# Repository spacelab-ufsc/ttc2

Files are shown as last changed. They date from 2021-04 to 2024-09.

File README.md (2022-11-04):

<h1 align="center">
    TELEMETRY, TRACKING AND COMMAND 2.0
    <br>
</h1>

<h4 align="center">Telemetry, Tracking and Command module (version 2) designed and developed by SpaceLab.</h4>

<p align="center">
    <a href="https://github.com/spacelab-ufsc/spacelab#versioning">
        
    </a>
    <a href="https://github.com/spacelab-ufsc/ttc2/releases">
        
    </a>
    <a href="https://github.com/spacelab-ufsc/ttc2/releases">
        
    </a>
    <a href="https://github.com/spacelab-ufsc/ttc2/commits/master">
        
    </a>
    <a href="https://github.com/spacelab-ufsc/ttc2/issues">
        
    </a>
    <a href="https://github.com/spacelab-ufsc/ttc2/graphs/contributors">
        
    </a>
</p>

<p align="center">
    <a href="#overview">Overview</a> •
    <a href="#license">License</a> •
    <a href="#releases">Releases</a> •
</p>

<p align="center">
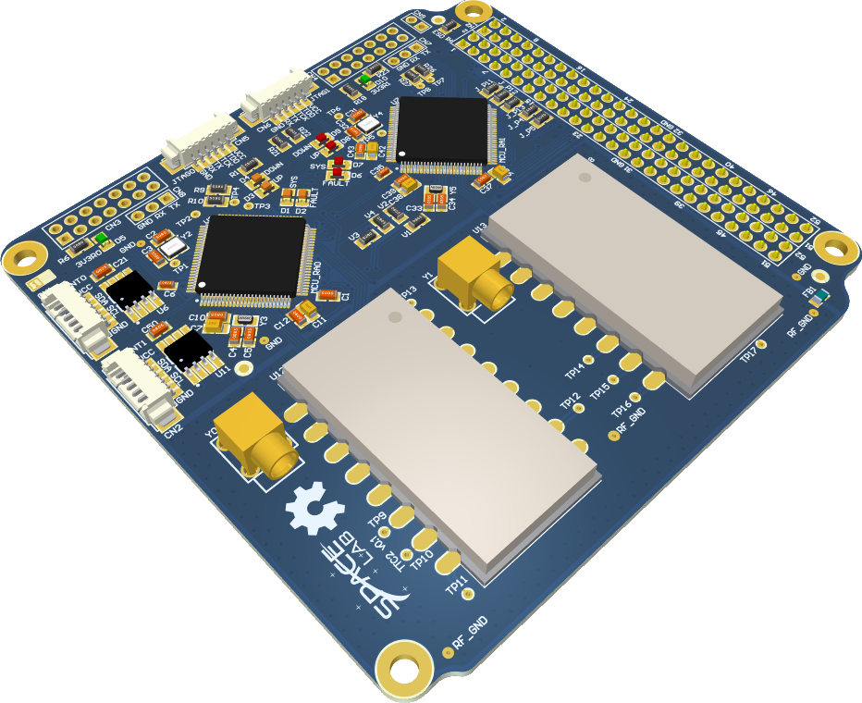
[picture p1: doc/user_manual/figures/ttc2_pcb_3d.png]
    
</p>

## Overview

The TTC (or TT&C) is the second generation communication module of the CubeSats from SpaceLab. It is responsible to make the communication between the earth (a ground station) and a satellite, and is divided in two sub-modules: Beacon and downlink/uplink.

## License

This project is open-source under three different licenses: GNU General Public License v3.0 for firmware sources, CERN Open Hardware License v2.0 for hardware files, and CC BY-SA 4.0 for the documentation. Some third-part files and libraries are subjected to their specific terms and licenses.

## Releases

The TTC 2.0 software and hardware releases are synchronized in order to garantee compatibility. Then, using diferent versions might lead to unpredictable behavior. Refer to the [documentation](https://github.com/spacelab-ufsc/ttc2/tree/master/doc) for compatibility notes.

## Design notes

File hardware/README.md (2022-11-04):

<h1 align="center">
    TTC2 HARDWARE
    <br>
</h1>

<h4 align="center">Telemetry, Tracking and Command module hardware project (sources, outputs, and documentation).</h4>

<p align="center">
    <a href="https://github.com/spacelab-ufsc/spacelab#versioning">
        
    </a>
    <a href="https://github.com/spacelab-ufsc/ttc2/releases">
        
    </a>
    <a href="https://github.com/spacelab-ufsc/ttc2/releases">
        
    </a>
    <a href="https://github.com/spacelab-ufsc/ttc2/commits/master">
        
    </a>
    <a href="https://github.com/spacelab-ufsc/ttc2/issues">
        
    </a>
    <a href="">
        
    </a>
    <a href="#license">
        
    </a>
    <a href="https://github.com/floripasat/ttc">
        
    </a>
</p>

<p align="center">
    <a href="#overview">Overview</a> •
    <a href="#architecture">Architecture</a> •
    <a href="#development">Development</a> •
    <a href="#version">Version</a> •
    <a href="#license">License</a> •
    <a href="#notes">Notes</a>
</p>

<p align="center">
    
    
</p>

## Overview

## Architecture

## Development

#### Manufacture

The folder [fabrication](https://github.com/spacelab-ufsc/ttc2/tree/master/hardware/fabrication) contain 3 "ready to go" files: the gerbers and nc_drills for manufacturing the board, the BOM with all required components, and the pick_place file for automated assembly. Additional files are avaliable in the [outputs](https://github.com/spacelab-ufsc/ttc2/tree/master/hardware/outputs) folder, which contain several useful files and documents, such as: 3D models, bill of materials, schematics, layout prints, and draftsman.

#### Assembly

The board has components that should not be soldered simultaneously. Refer to the [documentation](https://github.com/spacelab-ufsc/ttc2/tree/master/doc) in the "Assembly" chapter.

#### Power-on procedure

The board requires external supply from the PC-104 connector or the JTAG programmer interface. The following diagram present a simplified diagram of the board power. Refer to the [documentation](https://github.com/spacelab-ufsc/ttc2/tree/master/doc) in the "Instructions" chapter. 

#### Debugging

The debugging is performed through a serial UART port, using as default a baud rate of 115200, 1 stop bit, and no parity bit. The interface uses a log system standard to improve readability. Refer to the [documentation](https://github.com/spacelab-ufsc/obdh2/tree/master/doc) in the "Instructions" chapter.  

#### Testing

Automated testing is not avaliable yet.  

## Version

Refer to the [releases](https://github.com/spacelab-ufsc/ttc2/releases) page.

## License

This repository containing hardware files is licensed under CERN Open Hardware License, version 2.

## Notes

Project under development!

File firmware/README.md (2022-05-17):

<h1 align="center">
    <br>
    TTC 2.0 FIRMWARE
    <br>
</h1>

<h4 align="center">Telemetry, Tracking and Command module firmware project (sources, configs and documentation).</h4>

<p align="center">
    <a href="https://github.com/spacelab-ufsc/spacelab#versioning">
        
    </a>
    <a href="https://github.com/spacelab-ufsc/ttc2/releases">
        
    </a>
    <a href="https://github.com/spacelab-ufsc/ttc2/blob/dev_firmware/firmware/version.h">
        
    </a>
    <a href="https://github.com/spacelab-ufsc/ttc2/commits/master">
        
    </a>
    <a href="">
        
    </a>
    <a href="https://github.com/spacelab-ufsc/ttc2/blob/master/firmware/main.c">
        
    </a>
    <a href="">
        
    </a>
    <a href="#license">
        
    </a>
    <a href="https://github.com/spacelab-ufsc/ttc2/actions">
        
    </a>
</p>

<p align="center">
    <a href="#overview">Overview</a> •
    <a href="#dependencies">Dependencies</a> •
    <a href="#development">Development</a> •
    <a href="#version">Version</a> •
    <a href="#license">License</a>
</p>

<br>

## Overview

The TTC 2.0 board has two MSP430 low-power microcontrollers that runs the firmware application. It manages the others sub-modules within the board, synchronizes actions, handles communication with the Earth's segment, and manages the data flow. The programming language used is C and firmware was developed in the Code Composer Studio IDE (a.k.a. CCS). 

## Dependencies

* MSP430 DriverLib v2.91.11.01

## Development

#### Toolchain setup

The Code Composer Studio (CCS) v9.0, or later, can be downloaded [here](http://software-dl.ti.com/ccs/esd/documents/ccs_downloads.html). After downloaded, start the install process. For the TTC 2.0, only the *MSP430 Ultra Low Power MCUs* package is required. More instructions for Linux environment, click [here](https://software-dl.ti.com/ccs/esd/documents/ccs_linux_host_support.html).

#### Compiling and building
	
Clone [this repository](https://github.com/spacelab-ufsc/ttc2.git). After this, import the source project into CCS:
`File -> Import -> Code Composer Studio -> CCS Projects -> Select the source folder: ttc/firmware -> Leave 'Copy projects into workspace' unchecked / Finish`. Then, click in the Build button or press "Ctrl+B" to compile and build the sources. 

> Alternatively, it is possible to use the available makefile to import, compile and build the firmware in the linux environment. It is necessary to update the directories to correspond to those in the running machine, hit "make import" in the linux terminal and hit "make".

#### Debugging

Before deploying the program into the microcontroller using the JTAG interface, follow the [power-on procedures](https://github.com/spacelab-ufsc/ttc2/tree/dev_hardware/hardware#power-on-procedure). Using the [MSP-FET](http://www.ti.com/tool/MSP-FET) is possible to program the microcontroller and start a debug session, which allows full control of the firmware in execution. For that, with the project opened in the CCS, click in the "Debug" button or press "F11" to upload the code into the TTC 2.0 board.

Besides the JTAG, there is the debugging performed through a serial UART port, using as default a baud rate of 115200, 1 stop bit, and no parity bit. The interface uses a log system standard to improve readability. Refer to the [documentation](https://github.com/spacelab-ufsc/ttc2/tree/master/doc) in the "Instructions" chapter.

> Alternatively, it is possible to use the available makefile to perform the deployment of the firmware image into the microcontroller in the linux environment using the MSP-FET. It is necessary to follow the power-on procedures, connect the programmer and hit "make flash" in the terminal.

## Version

Refer to the [releases](https://github.com/spacelab-ufsc/ttc2/releases) page and the [version](https://github.com/spacelab-ufsc/ttc2/blob/master/firmware/version.h) file.

## License

The firmware of this project is licensed under GPLv3 license.

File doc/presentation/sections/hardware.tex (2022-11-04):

%
% design.tex
%
% Copyright (C) 2022 by SpaceLab.
%
% TTC 2.0 Critical Design Review
%
% This work is licensed under the Creative Commons Attribution-ShareAlike 4.0
% International License. To view a copy of this license,
% visit http://creativecommons.org/licenses/by-sa/4.0/.
%

%
% \brief Design slides.
%
% \author Gabriel Mariano Marcelino <gabriel.mm8@gmail.com>
% \author Miguel Boing <miguelboing13@gmail.com>
%
% \version 0.1.0
%
% \date 2022/07/28
%

\begin{frame}{Specifications}

    \begin{itemize}
        \item \textbf{Microcontroller}: MSP430F6659/MSP430F5659
        \item \textbf{Clock}: 32 MHz
        \item \textbf{Memories}:
        \begin{itemize}
            \item \textit{RAM}: 64 kB (SRAM)
            \item \textit{Flash}: 512 kB (code)
        \end{itemize}
        \item \textbf{Sensors}: Voltage, current and temperature
        \item \textbf{Modulation}: (G)FSK or (G)MSK
        \item \textbf{Baudrate}: 1200 to 9600 bps
        \item \textbf{Frequency}: 145-146 MHz, 435-438 MHz or 450 MHz bands
        \item \textbf{Protocol}: NGHam
        \item \textbf{Interfaces}: UART, I$^{2}$C and SPI
        \item \textbf{Mass}: 73 g
        \item PC-104 compatible
    \end{itemize}

\end{frame}

% #########################################################################
% #########################################################################

\begin{frame}{Electrical Block Diagram}

    \begin{figure}[!ht]
        \begin{center}
            
        \end{center}
    \end{figure}

\end{frame}

\begin{frame}{Schematics}

    Available at: \href{https://github.com/spacelab-ufsc/ttc2/tree/master/hardware/outputs/board_schematics}{\textcolor{blue}{\underline{https://github.com/spacelab-ufsc/ttc2}}}

    \begin{figure}[!ht]
        \begin{center}
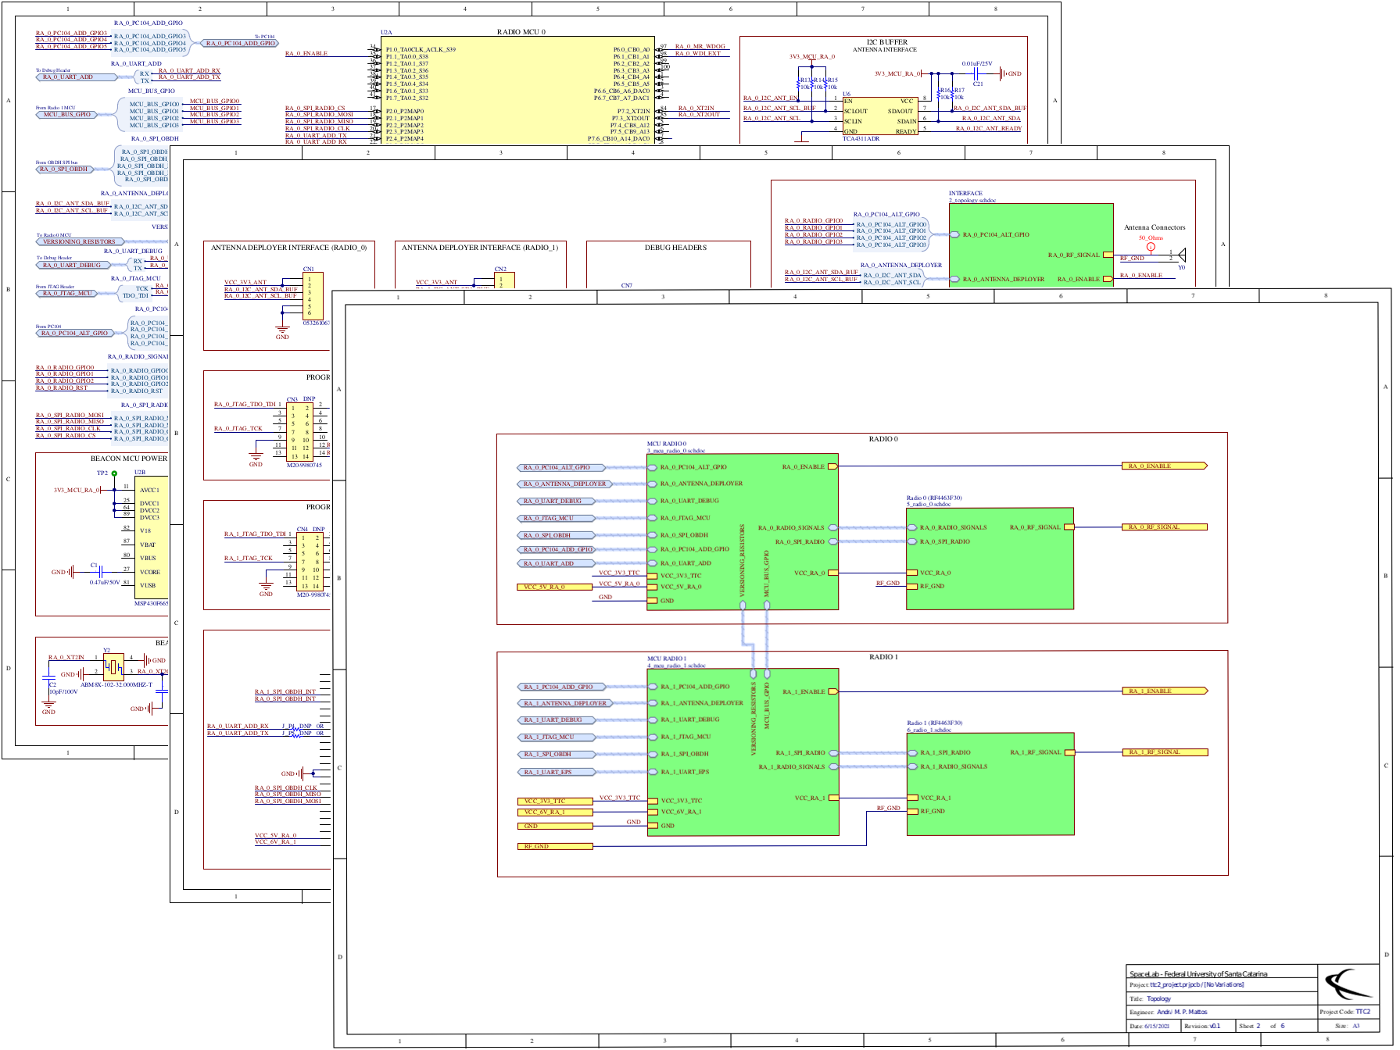
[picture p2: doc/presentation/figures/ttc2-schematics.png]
            
        \end{center}
    \end{figure}

\end{frame}

\begin{frame}{PCB Layout}

    Available at: \href{https://github.com/spacelab-ufsc/ttc2/tree/master/hardware/sources}{\textcolor{blue}{\underline{https://github.com/spacelab-ufsc/ttc2}}}

    \begin{columns}[t]
        \begin{column}[t]{0.5\textwidth}
            \begin{figure}[!ht]
                \begin{center}
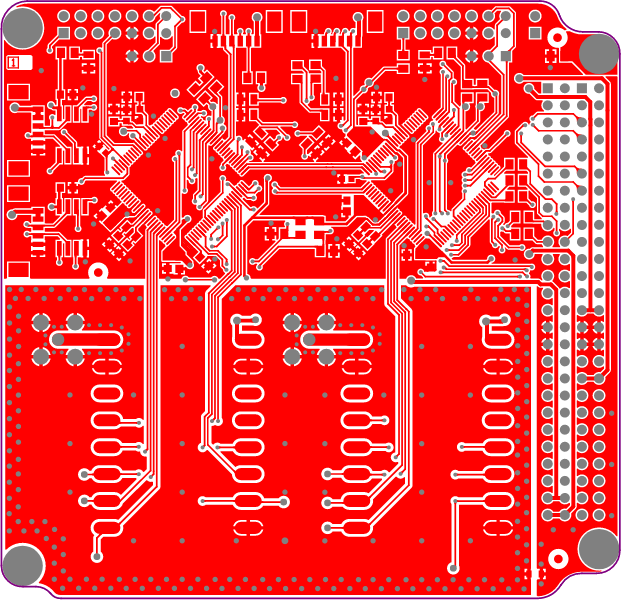
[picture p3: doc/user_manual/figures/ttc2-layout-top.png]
                    
                \end{center}
                \caption{Top side}
            \end{figure}
        \end{column}
        \begin{column}[t]{0.5\textwidth}
            \begin{figure}[!ht]
                \begin{center}
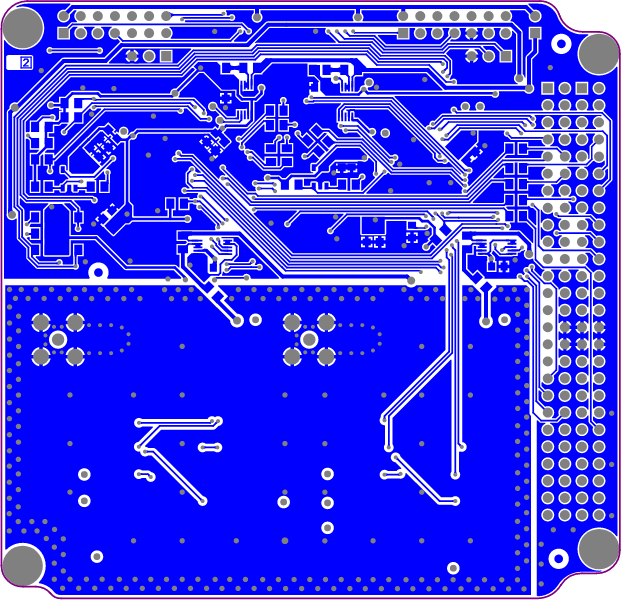
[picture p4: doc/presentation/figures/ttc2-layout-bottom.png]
                    
                \end{center}
                \caption{Bottom side}
            \end{figure}
        \end{column}
    \end{columns}

\end{frame}

\begin{frame}{3D Model}

    Available at: \href{https://github.com/spacelab-ufsc/ttc2/tree/master/hardware/outputs/board_3dmodels}{\textcolor{blue}{\underline{https://github.com/spacelab-ufsc/ttc2}}}

    \begin{figure}[!ht]
        \begin{center}
            
        \end{center}
    \end{figure}

\end{frame}

% #########################################################################
% #########################################################################

\begin{frame}{Power Consumption}

    \begin{itemize}
        \item Three separated voltage inputs: 3V3, 5V and 6V (microcontrollers and transceivers)
        \vspace{0.5cm}
        \item Power consumption\footnote{For one transceiver (there is two in TTC 2.0)}:
            \begin{itemize}
                \item Stand-by mode $\cong$ 83 mW
                \vspace{0.3cm}
                \item Transmission mode $\cong$ 2800 mW
                \vspace{0.3cm}
                \item Reception mode $\cong$ 163 mW
            \end{itemize}
    \end{itemize}

\end{frame}

% #########################################################################
% #########################################################################

\begin{frame}{Electrical Interfaces: PC-104}

\begin{table}[!h]\tiny
    \centering
    \begin{tabular}{cllll}
        \toprule[1.5pt]
        \textbf{Pin [A-B]} & \textbf{H1A}     & \textbf{H1B}     & \textbf{H2A}  & \textbf{H2B}  \\
        \midrule
        1-2                & -                & -                & -                & -                \\
        3-4                & -                & -                & -                & -                \\
        5-6                & -                & -                & RA\_1\_UART\_RX  & -                \\
        7-8                & GPIO\_6          & GPIO\_7          & RA\_1\_UART\_TX  & GPIO\_0          \\
        9-10               & RA\_1\_SPI\_INT  & RA\_1\_EN        & -                & -                \\
        11-12              & RA\_0\_SPI\_INT  & RA\_0\_EN        & RA\_1\_SPI\_MOSI & RA\_1\_SPI\_CLK  \\
        13-14              & -                & -                & RA\_1\_SPI\_CS   & RA\_1\_SPI\_MISO \\
        15-16              & -                & -                & -                & -                \\
        17-18              & -                & -                & -                & GPIO\_1          \\
        19-20              & -                & GPIO\_2          & -                & GPIO\_3          \\
        21-22              & -                & -                & -                & GPIO\_4          \\
        23-24              & -                & -                & -                & -                \\
        25-26              & -                & -                & -                & -                \\
        27-28              & -                & -                & VCC\_3V3         & VCC\_3V3         \\
        29-30              & GND              & GND              & GND              & GND              \\
        31-32              & GND              & GND              & GND              & GND              \\
        33-34              & -                & -                & -                & -                \\
        35-36              & RA\_0\_SPI\_CLK  & -                & VCC\_3V3\_ANT    & VCC\_3V3\_ANT    \\
        37-38              & RA\_0\_SPI\_MISO & -                & -                & -                \\
        39-40              & RA\_0\_SPI\_MOSI & RA\_0\_SPI\_CS   & -                & -                \\
        41-42              & -                & -                & -                & GPIO\_5          \\
        43-44              & -                & -                & -                & -                \\
        45-46              & -                & -                & -                & -                \\
        47-48              & -                & -                & -                & -                \\
        49-50              & VCC\_5V\_RA\_0   & VCC\_5V\_RA\_0   & -                & -                \\
        51-52              & VCC\_6V\_RA\_1   & VCC\_6V\_RA\_1   & -                & -                \\
        \bottomrule[1.5pt]
    \end{tabular}
    \label{tab:pc104-pins}
\end{table}

\end{frame}

\begin{frame}{Other Electrical Interfaces}

    \begin{table}[!htb]\tiny
        \centering
        \label{tab:icd}
        \begin{tabular}{lccl}
            \toprule[1.5pt]
            \textbf{Connector} & \textbf{Interface} & \textbf{Type} & \textbf{Pins} \\
            \midrule
            \multirow{6}{*}{CN1} & \multirow{6}{*}{I$^{2}$C} & \multirow{6}{*}{PicoBlade} & 3V3 \\
                                 &                           &                            & 3V3 \\
                                 &                           &                            & I2C\_SDA \\
                                 &                           &                            & I2C\_SCL \\
                                 &                           &                            & GND \\
                                 &                           &                            & GND \\
            \midrule
            \multirow{6}{*}{CN2} & \multirow{6}{*}{I$^{2}$C} & \multirow{6}{*}{PicoBlade} & 3V3 \\
                                 &                           &                            & 3V3 \\
                                 &                           &                            & I2C\_SDA \\
                                 &                           &                            & I2C\_SCL \\
                                 &                           &                            & GND \\
                                 &                           &                            & GND \\
            \bottomrule[1.5pt]
        \end{tabular}
    \end{table}

\end{frame}

\begin{frame}{Other Electrical Interfaces}

    \begin{table}[!htb]\tiny
        \centering
        \label{tab:icd}
        \begin{tabular}{lccl}
            \toprule[1.5pt]
            \textbf{Connector} & \textbf{Interface} & \textbf{Type} & \textbf{Pins} \\
            \midrule
            \multirow{14}{*}{CN3} & \multirow{14}{*}{JTAG} & \multirow{14}{*}{Pin Header} & TDO\_TDI \\
                                  &                        &                              & 3V3 \\
                                  &                        &                              & None \\
                                  &                        &                              & None \\
                                  &                        &                              & None \\
                                  &                        &                              & None \\
                                  &                        &                              & TCK \\
                                  &                        &                              & None \\
                                  &                        &                              & GND \\
                                  &                        &                              & None \\
                                  &                        &                              & None \\
                                  &                        &                              & UART\_TX \\
                                  &                        &                              & None \\
                                  &                        &                              & UART\_RX \\

            \bottomrule[1.5pt]
        \end{tabular}
    \end{table}

\end{frame}

\begin{frame}{Other Electrical Interfaces}

    \begin{table}[!htb]\tiny
        \centering
        \label{tab:icd}
        \begin{tabular}{lccl}
            \toprule[1.5pt]
            \textbf{Connector} & \textbf{Interface} & \textbf{Type} & \textbf{Pins} \\
            \midrule
            \multirow{14}{*}{CN4} & \multirow{14}{*}{JTAG} & \multirow{14}{*}{Pin Header} & TDO\_TDI \\
                                  &                        &                              & 3V3 \\
                                  &                        &                              & None \\
                                  &                        &                              & None \\
                                  &                        &                              & None \\
                                  &                        &                              & None \\
                                  &                        &                              & TCK \\
                                  &                        &                              & None \\
                                  &                        &                              & GND \\
                                  &                        &                              & None \\
                                  &                        &                              & None \\
                                  &                        &                              & UART\_TX \\
                                  &                        &                              & None \\
                                  &                        &                              & UART\_RX \\

            \bottomrule[1.5pt]
        \end{tabular}
    \end{table}

\end{frame}

\begin{frame}{Other Electrical Interfaces}

    \begin{table}[!htb]\tiny
        \centering
        \label{tab:icd}
        \begin{tabular}{lccl}
            \toprule[1.5pt]
            \textbf{Connector} & \textbf{Interface} & \textbf{Type} & \textbf{Pins} \\
            \midrule
            \multirow{6}{*}{CN5} & \multirow{6}{*}{JTAG} & \multirow{6}{*}{PicoBlade} & 3V3 \\
                                 &                       &                            & TDO\_TDI \\
                                 &                       &                            & TCK \\
                                 &                       &                            & UART\_TX \\
                                 &                       &                            & UART\_RX \\
                                 &                       &                            & GND \\
            \midrule
            \multirow{6}{*}{CN6} & \multirow{6}{*}{JTAG} & \multirow{6}{*}{PicoBlade} & 3V3 \\
                                 &                       &                            & TDO\_TDI \\
                                 &                       &                            & TCK \\
                                 &                       &                            & UART\_TX \\
                                 &                       &                            & UART\_RX \\
                                 &                       &                            & GND \\
            \midrule
            \multirow{3}{*}{CN7} & \multirow{3}{*}{UART} & \multirow{3}{*}{PinHeader} & TX \\
                                 &                       &                            & RX \\
                                 &                       &                            & GND \\
            \midrule
            \multirow{3}{*}{CN8} & \multirow{3}{*}{UART} & \multirow{3}{*}{PicoBlade} & TX \\
                                 &                       &                            & RX \\
                                 &                       &                            & GND \\
            \midrule
            \multirow{2}{*}{CN9} & \multirow{2}{*}{Jumper} & \multirow{2}{*}{Pin Header} & 3V3 \\
                                 &                         &                      & - \\
            \bottomrule[1.5pt]
        \end{tabular}
    \end{table}

\end{frame}

\begin{frame}{Other Electrical Interfaces}

    \begin{table}[!htb]\tiny
        \centering
        \label{tab:icd}
        \begin{tabular}{lccl}
            \toprule[1.5pt]
            \textbf{Connector} & \textbf{Interface} & \textbf{Type} & \textbf{Pins} \\
            \midrule
            \multirow{2}{*}{Y0} & \multirow{2}{*}{RF} & \multirow{2}{*}{MCX} & RF\_SIGNAL \\
                                &                     &                      & RF\_GND \\
            \midrule
            \multirow{2}{*}{Y1} & \multirow{2}{*}{RF} & \multirow{2}{*}{MCX} & RF\_SIGNAL \\
                                &                     &                      & RF\_GND \\
            \bottomrule[1.5pt]
        \end{tabular}
    \end{table}

\end{frame}

\begin{frame}{Dimensions}

    \begin{figure}[!ht]
        \begin{center}
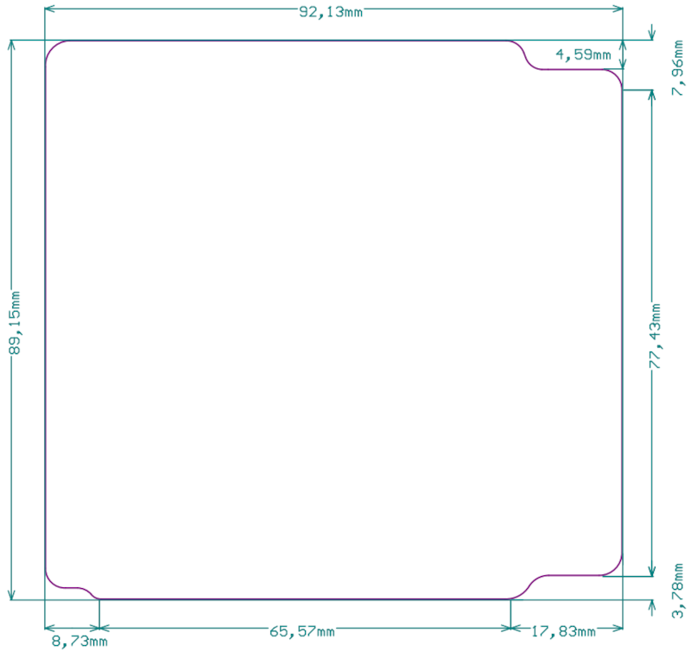
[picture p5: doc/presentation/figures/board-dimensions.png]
            
        \end{center}
    \end{figure}

\end{frame}

\begin{frame}{Voltage/Current Sensors}

    \begin{itemize}
        \item Voltage, current and power sensor
        \vspace{0.3cm}
        \item Quantity: 4 (one per radio module and one per microncontroller circuit)
        \vspace{0.3cm}
        \item Texas Instruments INA226AQDGSRQ1
        \vspace{0.3cm}
        \item I$^{2}$C Interface
        \vspace{0.3cm}
    \end{itemize}

\end{frame}

\begin{frame}{External Watchdog}

    \begin{itemize}
        \item IC: Texas Instruments TPS3823
        \vspace{0.5cm}
        \item Voltage monitor with a watchdog timer feature
        \vspace{0.5cm}
        \item Timeout period: $1600\ ms$
        \vspace{0.5cm}
        \item Reset period: $100\ ms$
    \end{itemize}

\end{frame}

\begin{frame}{Transceiver}

    \begin{itemize}
        \item \href{https://www.nicerf.com/products/detail/1w-rf-module-rf4463f30.html}{\textcolor{blue}{\underline{NiceRF RF4463F30}}}
        \item Based on \href{https://www.silabs.com/wireless/proprietary/ezradiopro-sub-ghz-ics/device.si4463?tab=specs}{\textcolor{blue}{\underline{Si4463}}} transceiver
        \item Integrated power amplifier and RF switch (single antenna)
        \item Half-Duplex
        \item Output power: 30 dBm
        \item SPI Interface
    \end{itemize}
    \begin{figure}[!ht]
        \begin{center}
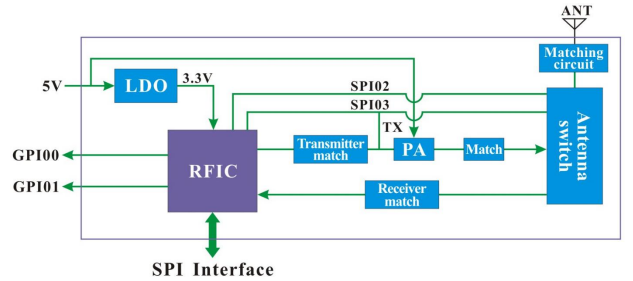
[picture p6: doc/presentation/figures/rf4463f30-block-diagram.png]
            
        \end{center}
    \end{figure}

\end{frame}

\begin{frame}{Flight Model Specs. and Preparation}

    \begin{itemize}
        \item \textbf{PCB specs.}: IPC 6012 Class 3
        \vspace{0.3cm}
        \item \textbf{PCB thickness}: 1,6 mm
        \vspace{0.3cm}
        \item \textbf{Material}: TG170 FR-4
        \vspace{0.3cm}
        \item \textbf{Surface finish}: ENIG
        \vspace{0.3cm}
        \item \textbf{Board finish}: Conformal coating application
    \end{itemize}

\end{frame}

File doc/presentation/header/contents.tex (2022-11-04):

%
% contents.tex
%
% Copyright (C) 2022 by SpaceLab.
%
% TTC 2.0 Module
%
% This work is licensed under the Creative Commons Attribution-ShareAlike 4.0
% International License. To view a copy of this license,
% visit http://creativecommons.org/licenses/by-sa/4.0/.
%

%
% \brief Table of contents.
%
% \author Gabriel Mariano Marcelino <gabriel.mm8@gmail.com>
% \author Miguel Boing <miguelboing13@gmail.com>
%
% \version 0.1.0
%
% \date 2022/06/24
%

\begin{frame}
    \frametitle{Summary}
    \tableofcontents
\end{frame}

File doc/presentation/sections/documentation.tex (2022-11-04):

%
% documentation.tex
%
% Copyright (C) 2022 by SpaceLab.
%
% TTC 2.0 Module
%
% This work is licensed under the Creative Commons Attribution-ShareAlike 4.0
% International License. To view a copy of this license,
% visit http://creativecommons.org/licenses/by-sa/4.0/.
%

%
% \brief Documentation slides.
%
% \author Gabriel Mariano Marcelino <gabriel.mm8@gmail.com>
% \author Miguel Boing <miguelboing13@gmail.com>
%
% \version 0.1.0
%
% \date 2022/08/07
%

\begin{frame}{Documentation}

    \begin{itemize}
        \item User manual (PDF)
        \vspace{0.4cm}
        \item This presentation
        \vspace{0.4cm}
        \item Schematics
        \vspace{0.4cm}
        \item Firmware: Doxygen
    \end{itemize}

\end{frame}

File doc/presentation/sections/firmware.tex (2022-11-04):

%
% firmware.tex
%
% Copyright (C) 2022 by SpaceLab.
%
% TTC 2.0 Module
%
% This work is licensed under the Creative Commons Attribution-ShareAlike 4.0
% International License. To view a copy of this license,
% visit http://creativecommons.org/licenses/by-sa/4.0/.
%

%
% \brief Firmware project slides.
%
% \author Gabriel Mariano Marcelino <gabriel.mm8@gmail.com>
% \author Miguel Boing <miguelboing13@gmail.com>
%
% \version 0.1.0
%
% \date 2022/07/28
%

\begin{frame}{Overview}

    \begin{columns}[t]
        \begin{column}[t]{0.6\textwidth}
            \begin{itemize}
                \vspace{1cm}
                \item Language: C
                \vspace{0.5cm}
                \item OS: FreeRTOS v10.2.1
            \end{itemize}
        \end{column}
        \begin{column}[t]{0.4\textwidth}
            \begin{figure}[!ht]
                \begin{center}
                    
                \end{center}
            \end{figure}
        \end{column}
    \end{columns}

\end{frame}

% #########################################################################
% #########################################################################

\begin{frame}{System Tasks}

\begin{table}[!h]\scriptsize
    \centering
    \label{tab:firmware-tasks}
    \begin{tabular}{lccccc}
        \toprule[1.5pt]
        \textbf{Name}          & \textbf{Priority} & \textbf{Initial delay [ms]} & \textbf{Period [ms]} & \textbf{Stack [bytes]} \\
        \midrule
        Command Processing     & Highest & 0     & 100       & 500 \\
        Heartbeat              & Lowest  & 0     & 500       & 160 \\
        Housekeeping           & Medium  & 2000  & 10000     & 160 \\
        Radio Reset            & High    & 60000 & 60000     & 128 \\
        Startup                & Medium  & 0     & Aperiodic & 128 \\
        System Reset           & Medium  & 0     & 36000000  & 128 \\
        Time Control           & Medium  & 1000  & 1000      & 128 \\
        Uplink                 & Highest & 2000  & 500       & 500 \\
        Watchdog Reset         & Lowest  & 0     & 100       & 150 \\
        \bottomrule[1.5pt]
    \end{tabular}
\end{table}

\end{frame}

\begin{frame}{System Tasks}

    \begin{itemize}
        \item \textbf{Command Processing}: Process incomming commands (physical interfaces).
        \item \textbf{Heartbeat}: Blinks a status LED at a rate of 1 Hz.
        \item \textbf{Housekeeping}: This task manages the general operation of
the TTC.
        \item \textbf{Radio Reset}: Resets the radio at 600 seconds.
        \item \textbf{Startup}: Initializes the TTC 2.0 module.
        \item \textbf{System Reset}: Resets the microcontroller by software at every 10 hours.
        \item \textbf{Time Control}: Manages the system time.
        \item \textbf{Uplink}: Monitors radio for upcoming packages and stores it in memory.
        \item \textbf{Watchdog Reset}: Resets the watchdog timers at every 100 miliseconds.
    \end{itemize}

 \end{frame}

% #########################################################################
% #########################################################################

\begin{frame}{System Parameters}

\begin{table}[!htb]\tiny
    \centering
    \label{tab:vars-and-pars}
    \begin{tabular}{cll}
        \toprule[1.5pt]
        \textbf{ID} & \textbf{Name/Description} & \textbf{Type}\\
        \midrule
        0   & Device ID (0xCC2A or 0xCC2B)                                      & uint16 \\
        1   & Hardware version                                                  & uint8 \\
        2   & Firmware version (ex.: ``v1.2.3''' = 0x00010203)                  & uint32 \\
        3   & Time counter in millseconds                                       & uint32 \\
        4   & Reset counter                                                     & uint16 \\
        5   & Last reset cause:                                                 & uint8 \\
        6   & Input voltage of the $\mu$C in mV                                 & uint16 \\
        7   & Input current of the $\mu$C in mA                                 & uint16 \\
        8   & Temperature of the $\mu$C in K                                    & uint16 \\
        9   & Input voltage of the radio in mV                                  & uint16 \\
        10  & Input current of the radio in mA                                  & uint16 \\
        11  & Temperature of the radio in K                                     & uint16 \\
        12  & Last valid command (uplink packet ID)                             & uint8 \\
        13  & RSSI of the last valid telecommand                                & uint16 \\
        14  & Temperature of the antenna module in K                            & uint16 \\
        15  & Antenna module status bits                                        & uint16 \\
        16  & Antenna deployment status                                         & uint8 \\
        17  & Antenna deployment hibernation                                    & uint8 \\
        18  & TX enable                                                         & uint8 \\
        19  & TX packet counter                                                 & uint32 \\
        20  & RX packet counter (valid packets)                                 & uint32 \\
        21  & TX packets available in the FIFO buffer                           & uint8 \\
        22  & RX packets available in the FIFO buffer                           & uint8 \\
        23  & Number of bytes of the first available packet in the RX buffer    & uint16 \\
        \bottomrule[1.5pt]
    \end{tabular}
\end{table}

\end{frame}

\begin{frame}{Commands}

\begin{table}[!htb]\scriptsize
    \centering
    \label{tab:vars-and-pars}
    \begin{tabular}{cll}
        \toprule[1.5pt]
        \textbf{ID} & \textbf{Command} & \textbf{Parameters}\\
        \midrule
        1   & Read parameter              & Parameter ID \\
        2   & Write parameter             & Parameter ID + Parameter value \\
        3   & Transmit packet             & Data to transmit (payload of the NGHam packet) \\
        4   & Read first available packet & None \\
        \bottomrule[1.5pt]
    \end{tabular}
\end{table}

\end{frame}

% #########################################################################
% #########################################################################

\begin{frame}{Development Environment}

    \begin{columns}[t]
        \begin{column}[t]{0.6\textwidth}
            \begin{itemize}
                \vspace{0.4cm}
                \item Hardware: Engineering Model (EM)
                \vspace{0.4cm}
                \item Programmer: Texas Instruments MSP-FET programmer
                \vspace{0.4cm}
                \item IDE/Compiler: Code Composer Studio
                \vspace{0.4cm}
            \end{itemize}
        \end{column}
        \begin{column}[t]{0.5\textwidth}
            \vspace{1cm}
            \begin{figure}[!ht]
                \begin{center}
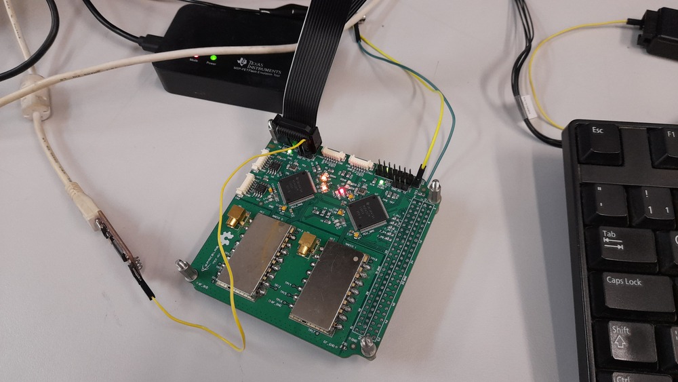
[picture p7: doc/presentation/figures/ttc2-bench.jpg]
                    
                \end{center}
            \end{figure}
        \end{column}
    \end{columns}

\end{frame}

% #########################################################################
% #########################################################################

\begin{frame}{Verification \& Validation}

    \begin{itemize}
        \item Unit tests framework: \href{https://cmocka.org/}{\textcolor{blue}{\underline{CMocka}}}
        \vspace{0.5cm}
        \item Static analysis tool: \href{https://cppcheck.sourceforge.io/}{\textcolor{blue}{\underline{CppCheck}}}
        \vspace{0.5cm}
        \item Code style standard: \href{https://www.misra.org.uk/}{\textcolor{blue}{\underline{MISRA-C 2012}}}
    \end{itemize}

\end{frame}

\begin{frame}{Verification \& Validation: TDD Flow}

    \begin{figure}[!ht]
        \begin{center}
            
        \end{center}
    \end{figure}

\end{frame}

\begin{frame}{Verification \& Validation: Development Flow}

    \begin{figure}[!ht]
        \begin{center}
            
        \end{center}
    \end{figure}

\end{frame}

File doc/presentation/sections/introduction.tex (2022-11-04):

%
% introduction.tex
%
% Copyright (C) 2022 by SpaceLab.
%
% TTC 2.0 Critical Design Review
%
% This work is licensed under the Creative Commons Attribution-ShareAlike 4.0
% International License. To view a copy of this license,
% visit http://creativecommons.org/licenses/by-sa/4.0/.
%

%
% \brief Introduction slides.
%
% \author Gabriel Mariano Marcelino <gabriel.mm8@gmail.com>
% \author Miguel Boing <miguelboing13@gmail.com>
%
% \version 0.1.0
%
% \date 2022/07/28
%

\begin{frame}{Overview}

    \begin{columns}[t]
        \begin{column}[t]{0.5\textwidth}
            \begin{itemize}
                \item Telemetry, Tracking and Command (TTC) module for small satellites like CubeSats
                \vspace{0.5cm}
                \item Project name: ``\textit{TTC 2.0}''
                \vspace{0.5cm}
                \item Fully open source
                \vspace{0.5cm}
                \item Based on FloripaSat-1 heritage
            \end{itemize}
        \end{column}
        \begin{column}[t]{0.5\textwidth}
            \begin{figure}[!ht]
                \begin{center}
                    
                \end{center}
            \end{figure}
        \end{column}
    \end{columns}

\end{frame}

% #########################################################################
% #########################################################################

\begin{frame}{Product Tree}

    \begin{figure}[!ht]
        \begin{center}
            
        \end{center}
    \end{figure}

\end{frame}

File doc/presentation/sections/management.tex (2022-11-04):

%
% management.tex
%
% Copyright (C) 2022 by SpaceLab.
%
% TTC 2.0 Critical Design Review
%
% This work is licensed under the Creative Commons Attribution-ShareAlike 4.0
% International License. To view a copy of this license,
% visit http://creativecommons.org/licenses/by-sa/4.0/.
%

%
% \brief Project management slides.
%
% \author Gabriel Mariano Marcelino <gabriel.mm8@gmail.com>
% \author Miguel Boing <miguelboing13@gmail.com>
%
% \version 0.1.0
%
% \date 2022/07/28
%

\begin{frame}{Project Management}

    \begin{itemize}
        \item Activities and tasks: Public GitHub issues/project
        \vspace{0.25cm}
        \item Source files and versioning control: \href{https://github.com/spacelab-ufsc/obdh2}{\textcolor{blue}{Git repository}} with three development branches:
            \begin{itemize}
                \item \textit{dev\_doc}: Documentation
                \item \textit{dev\_hardware}: Hardware project
                \item \textit{dev\_firmware}: Firmware project
            \end{itemize}
    \end{itemize}

    \begin{figure}[!ht]
        \begin{center}
            
        \end{center}
    \end{figure}

\end{frame}

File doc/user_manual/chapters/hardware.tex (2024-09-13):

%
% hardware.tex
%
% Copyright The TTC 2.0 Contributors.
%
% TTC 2.0 Documentation
%
% This work is licensed under the Creative Commons Attribution-ShareAlike 4.0
% International License. To view a copy of this license,
% visit http://creativecommons.org/licenses/by-sa/4.0/.
%

%
% \brief Hardware project chapter.
%
% \author Gabriel Mariano Marcelino <gabriel.mm8@gmail.com>
%
% \version 1.0.0
%
% \date 2021/04/02
%

\chapter{Hardware} \label{ch:hardware}

This chapter presents a description of the hardware project of the TTC 2.0 module. As the primary reference, a block diagram can be seen in \autoref{fig:hardware-diagram}. Also, a 3D model of both sides of the PCB is available in \autoref{fig:ttc2-3d-surface}.

\begin{figure}[!ht]
	\begin{center}
		
		\caption{Block diagram of the TTC 2.0 hardware.}
		\label{fig:hardware-diagram}
	\end{center}
\end{figure}

\begin{figure}[!ht]
    \begin{center}
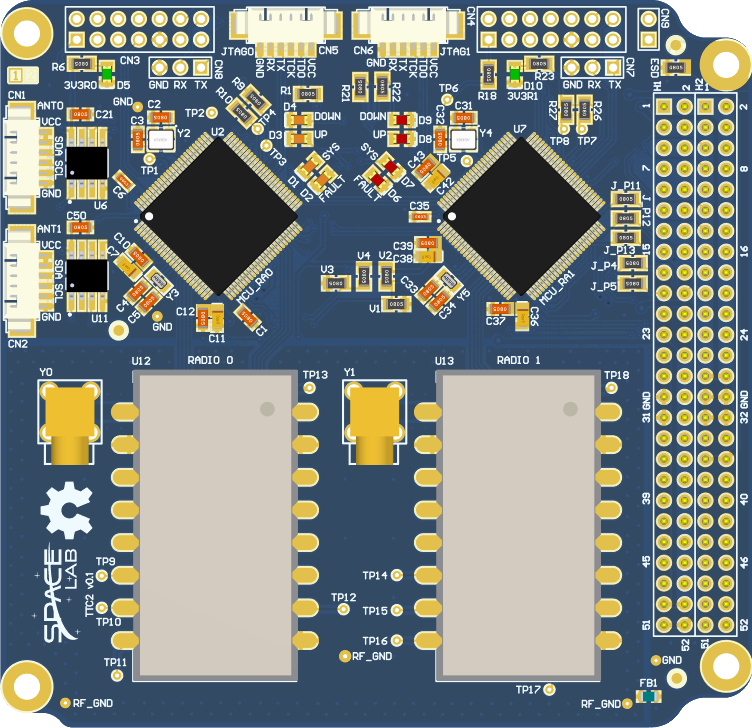
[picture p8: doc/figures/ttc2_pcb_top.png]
        \subfigure[Top side.\label{fig:ttc2-pcb-top}]{}
        ~
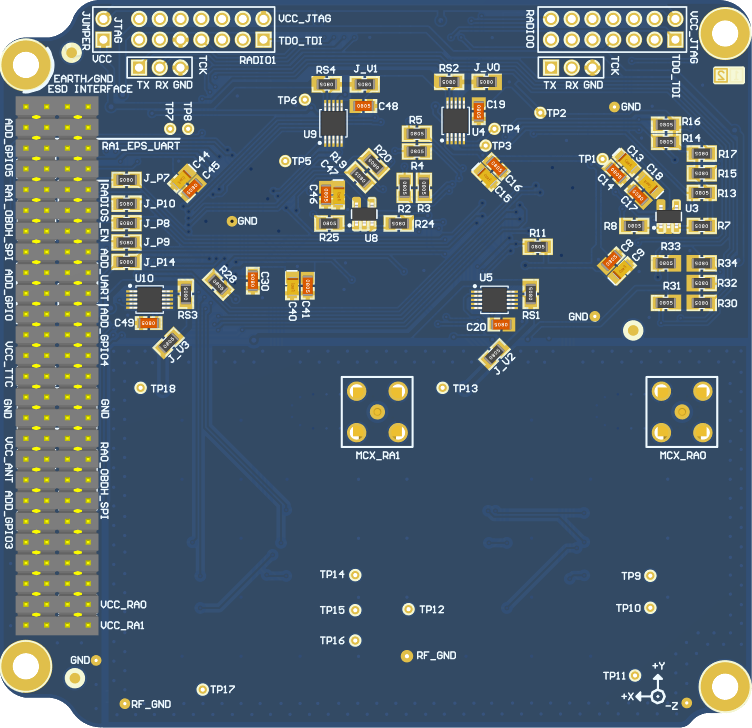
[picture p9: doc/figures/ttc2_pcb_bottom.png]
        \subfigure[Bottom side.\label{fig:ttc2-pcb-bottom}]{}
        \caption{Top and bottom sides of the TTC 2.0 board.}
        \label{fig:ttc2-3d-surface}
    \end{center}
\end{figure}

The following sections present a further description of the hardware project.

\section{Specifications}

The TTC 2.0 has two microcontrollers (MSP430FR6659) that run at a clock of 32 MHz, a RAM of 64 kB (SRAM), a flash memory of 512 kB for code storage, and another one of 128 kB for data storage. The TTC 2.0 also has current, voltage, and temperature sensors and two radio modules for RF communication. A brief description of the general specifications of the TTC 2.0 module is available below:

\begin{itemize}
    \item \textbf{Microcontroller}: MSP430F6659
    \item \textbf{Clock}: 32 MHz
    \item \textbf{Memories}:
    \begin{itemize}
        \item RAM: 64 kB (SRAM)
        \item Flash: 512 kB (code) and 128 kB (storage)
    \end{itemize}
    \item \textbf{Sensors}: Voltage, current and temperature
    \item \textbf{Modulation}: (G)FSK and/or (G)MSK
    \item \textbf{Baudrate}: 1200 to 9600 bps
    \item \textbf{Frequency}: 145-146, 400-402, 435-438, or 468-469 MHz bands
    \item \textbf{Protocol}: NGHam
    \item \textbf{Interfaces}: UART, I$^{2}$C and SPI
    \item \textbf{Mass}: 73 g
    \item \textbf{Main bus}: PC-104 standard
\end{itemize}

\section{Electrical interfaces}

Below is a description of all available electrical interfaces of the TTC 2.0 module. The interfaces can be divided into PC-104 bus and dedicated interfaces.

\subsection{PC-104 bus}

The connector PC-104 is a junction of two double rows 26 pin headers (\textit{SSW-126-04-G-D} by default). These connectors create a solid 104-pin interconnection across the different satellite modules. \autoref{tab:pc104-pinout} provides the connector pinout\footnote{This pinout is simplified since additional interfaces were omitted.} for the pins that are connected to the module. A reference of the pin's position can also be seen in \autoref{fig:pc104-ref-diagram}, and a description of the signal is available in \autoref{tab:pc104-signals}.

\begin{figure}[!ht]
    \begin{center}
        
        \caption{Reference diagram of the PC-104 bus (top view of a generic module).}
        \label{fig:pc104-ref-diagram}
    \end{center}
\end{figure}

\begin{table}[!ht]
    \centering
    \begin{tabular}{cllll}
        \toprule[1.5pt]
        \textbf{Pin Row}   & \textbf{H1 Odd}  & \textbf{H1 Even} & \textbf{H2 Odd}  & \textbf{H2 Even} \\
        \midrule
        1-2                & -                & -                & -                & -                \\
        3-4                & -                & -                & -                & -                \\
        5-6                & -                & -                & RA\_1\_UART\_RX  & -                \\
        7-8                & GPIO\_6          & GPIO\_7          & RA\_1\_UART\_TX  & GPIO\_0          \\
        9-10               & RA\_1\_SPI\_INT  & RA\_1\_EN        & -                & -                \\
        11-12              & RA\_0\_SPI\_INT  & RA\_0\_EN        & RA\_1\_SPI\_MOSI & RA\_1\_SPI\_CLK  \\
        13-14              & -                & -                & RA\_1\_SPI\_CS   & RA\_1\_SPI\_MISO \\
        15-16              & -                & -                & -                & -                \\
        17-18              & -                & -                & -                & GPIO\_1          \\
        19-20              & -                & GPIO\_2          & -                & GPIO\_3          \\
        21-22              & -                & -                & -                & GPIO\_4          \\
        23-24              & -                & -                & -                & -                \\
        25-26              & -                & -                & -                & -                \\
        27-28              & -                & -                & VCC\_3V3         & VCC\_3V3         \\
        29-30              & GND              & GND              & GND              & GND              \\
        31-32              & GND              & GND              & GND              & GND              \\
        33-34              & -                & -                & -                & -                \\
        35-36              & RA\_0\_SPI\_CLK  & -                & VCC\_3V3\_ANT    & VCC\_3V3\_ANT    \\
        37-38              & RA\_0\_SPI\_MISO & -                & -                & -                \\
        39-40              & RA\_0\_SPI\_MOSI & RA\_0\_SPI\_CS   & -                & -                \\
        41-42              & -                & -                & -                & GPIO\_5          \\
        43-44              & -                & -                & -                & -                \\
        45-46              & -                & -                & -                & -                \\
        47-48              & -                & -                & -                & -                \\
        49-50              & VCC\_5V\_RA\_0   & VCC\_5V\_RA\_0   & -                & -                \\
        51-52              & VCC\_6V\_RA\_1   & VCC\_6V\_RA\_1   & -                & -                \\
        \bottomrule[1.5pt]
    \end{tabular}
    \caption{PC-104 bus pinout.}
    \label{tab:pc104-pinout}
\end{table}

\begin{table}[!ht]
    \centering
    \begin{tabular}{lL{0.3\textwidth}l}
        \toprule[1.5pt]
        \textbf{Signal}  & \textbf{Pin(s)}                  & \textbf{Description} \\
        \midrule
        GND              & H1-29/30/31/32, H2-29/30/31/32   & Ground reference                      \\
        VCC\_3V3         & H2-27, H2-28                     & TTC power supply (3,3 V)              \\
        VCC\_3V3\_ANT    & H2-35, H2-36                     & Antenna power supply (3,3 V)          \\
        VCC\_5V\_RA\_0   & H1-49, H1-50                     & Radio 0 power supply (5 V)            \\
        VCC\_6V\_RA\_1   & H1-51, H1-52                     & Radio 1 power supply (6 V)            \\
        RA\_0\_SPI\_CLK  & H1-35                            & CLK signal of the radio 0 SPI bus     \\
        RA\_0\_SPI\_MISO & H1-37                            & MISO signal of the radio 0 SPI bus    \\
        RA\_0\_SPI\_MOSI & H1-39                            & MOSI signal of the radio 0 SPI bus    \\
        RA\_0\_SPI\_CS   & H1-40                            & CS signal of the radio 0 SPI bus      \\
        RA\_0\_SPI\_INT  & H1-11                            & INT signal of the radio 0 SPI bus     \\
        RA\_1\_SPI\_CLK  & H2-12                            & CLK signal of the radio 0 SPI bus     \\
        RA\_1\_SPI\_MISO & H2-14                            & MISO signal of the radio 0 SPI bus    \\
        RA\_1\_SPI\_MOSI & H2-11                            & MOSI signal of the radio 0 SPI bus    \\
        RA\_1\_SPI\_CS   & H1-13                            & CS signal of the radio 0 SPI bus      \\
        RA\_1\_SPI\_INT  & H1-9                             & INT signal of the radio 0 SPI bus     \\
        RA\_1\_UART\_RX  & H2-5                             & RX signal of the radio 1 UART         \\
        RA\_1\_UART\_TX  & H2-7                             & TX signal of the radio 1 UART         \\
        RA\_0\_EN        & H1-11                            & Radio 0 power enable                  \\
        RA\_1\_EN        & H1-9                             & Radio 1 power enable                  \\
        GPIO\_N          & H1-7/8/19, H2-8/18/20/22/42      & GPIO pin (not used)                   \\
        \bottomrule[1.5pt]
    \end{tabular}
    \caption{PC-104 bus signal description.}
    \label{tab:pc104-signals}
\end{table}

This project's distribution pattern of pins is a mix of multiple patterns from CubeSat module manufacturers, like GomSpace, ISISpace, and EnduroSat. Some pins are positioned to attend to specific project requirements; this way, it is possible that the adopted pattern is only partially compatible with some commercial modules or other custom projects.

\subsection{Dedicated electrical interfaces}

The module also contains other electrical interfaces through pin headers and PicoBlade connectors that are used to flash code and as debug port of microcontrollers (CN5, CN3, CN4, CN6) and serial communication for a status report and log messages (CN7, CN8). The C9 connector switches the TTC 2.0 power supply to the MSP-FET. The CN1 and CN2 are antenna interfaces (I$^{2}$C bus and power), and Y0, Y1 are MCX connectors to be used as the RF interface with the antennas. More details of each of these connectors, like the pinout, can be seen in \autoref{tab:icd}.

\begin{longtable}[c]{lcccl}
    \toprule[1.5pt]
    \textbf{Connector} & \textbf{Image} & \textbf{Interface} & \textbf{Type} & \textbf{Pins} \\
    \midrule
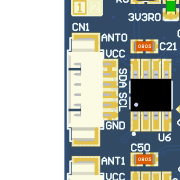
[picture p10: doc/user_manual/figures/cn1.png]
    \multirow{10}{*}{CN1} & \multirow{10}{*}{\raisebox{-\totalheight}{}} & \multirow{10}{*}{I$^{2}$C} & \multirow{10}{*}{PicoBlade} &  \\
                          &  &                           &                            &  \\
                          &  &                           &                            & 3V3 \\
                          &  &                           &                            & 3V3 \\
                          &  &                           &                            & I2C\_SDA \\
                          &  &                           &                            & I2C\_SCL \\
                          &  &                           &                            & GND \\
                          &  &                           &                            & GND \\
                          &  &                           &                            &  \\
                          &  &                           &                            &  \\
    \midrule
    \multicolumn{5}{r}{\textit{Continues on next page}} \\
    \pagebreak
    \midrule
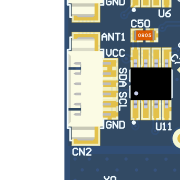
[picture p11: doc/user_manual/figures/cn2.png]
    \multirow{10}{*}{CN2} & \multirow{10}{*}{\raisebox{-\totalheight}{}} & \multirow{10}{*}{I$^{2}$C} & \multirow{10}{*}{PicoBlade} &  \\
                          &  &                           &                            &  \\
                          &  &                           &                            & 3V3 \\
                          &  &                           &                            & 3V3 \\
                          &  &                           &                            & I2C\_SDA \\
                          &  &                           &                            & I2C\_SCL \\
                          &  &                           &                            & GND \\
                          &  &                           &                            & GND \\
                          &  &                           &                            & \\
                          &  &                           &                            & \\
    \midrule
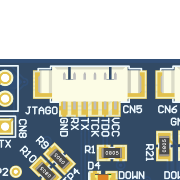
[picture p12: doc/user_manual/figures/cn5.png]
    \multirow{10}{*}{CN5} & \multirow{10}{*}{\raisebox{-\totalheight}{}} & \multirow{10}{*}{JTAG} & \multirow{10}{*}{PicoBlade} &  \\
                          &  &                           &                            &  \\
                          &  &                           &                            & 3V3\_JTAG \\
                          &  &                           &                            & TDO\_TDI \\
                          &  &                           &                            & TCK \\
                          &  &                           &                            & UART\_TX \\
                          &  &                           &                            & UART\_RX \\
                          &  &                           &                            & GND \\
                          &  &                           &                            & \\
                          &  &                           &                            & \\
    \midrule
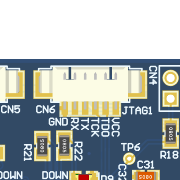
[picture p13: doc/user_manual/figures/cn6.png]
    \multirow{10}{*}{CN6} & \multirow{10}{*}{\raisebox{-\totalheight}{}} & \multirow{10}{*}{JTAG} & \multirow{10}{*}{PicoBlade} &  \\
                          &  &                           &                            &  \\
                          &  &                           &                            & 3V3\_JTAG \\
                          &  &                           &                            & TDO\_TDI \\
                          &  &                           &                            & TCK \\
                          &  &                           &                            & UART\_TX \\
                          &  &                           &                            & UART\_RX \\
                          &  &                           &                            & GND \\
                          &  &                           &                            & \\
                          &  &                           &                            & \\
    \midrule
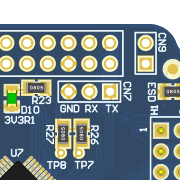
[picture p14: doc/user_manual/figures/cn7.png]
    \multirow{10}{*}{CN7} & \multirow{10}{*}{\raisebox{-\totalheight}{}} & \multirow{10}{*}{UART} & \multirow{10}{*}{PinHeader} &  \\
                          &  &                           &                            &  \\
                          &  &                           &                            &  \\
                          &  &                           &                            & TX \\
                          &  &                           &                            & RX \\
                          &  &                           &                            & GND \\
                          &  &                           &                            &  \\
                          &  &                           &                            &  \\
                          &  &                           &                            &  \\
                          &  &                           &                            &  \\
    \midrule
    \multicolumn{5}{r}{\textit{Continues on next page}} \\
    \pagebreak
    \midrule
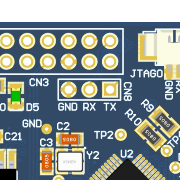
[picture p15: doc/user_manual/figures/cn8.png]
    \multirow{10}{*}{CN8} & \multirow{10}{*}{\raisebox{-\totalheight}{}} & \multirow{10}{*}{UART} & \multirow{10}{*}{PicoBlade} &  \\
                          &  &                           &                            &  \\
                          &  &                           &                            &  \\
                          &  &                           &                            & TX \\
                          &  &                           &                            & RX \\
                          &  &                           &                            & GND \\
                          &  &                           &                            &  \\
                          &  &                           &                            &  \\
                          &  &                           &                            &  \\
                          &  &                           &                            &  \\
    \midrule
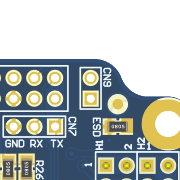
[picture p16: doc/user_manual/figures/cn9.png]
    \multirow{10}{*}{CN9}  & \multirow{10}{*}{\raisebox{-\totalheight}{}} & \multirow{10}{*}{Jumper} & \multirow{10}{*}{Pin Header} &  \\
                          &  &                           &                            &  \\
                          &  &                           &                            &  \\
                          &  &                           &                            &  \\
                          &  &                           &                            & 3V3\_JTAG \\
                          &  &                           &                            & 3V3 \\
                          &  &                           &                            &  \\
                          &  &                           &                            &  \\
                          &  &                           &                            &  \\
                          &  &                           &                            &  \\
    \midrule
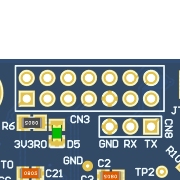
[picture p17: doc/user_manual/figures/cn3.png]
    \multirow{14}{*}{CN3} & \multirow{14}{*}{\raisebox{-\totalheight}{}} & \multirow{14}{*}{JTAG} & \multirow{14}{*}{Pin Header} & TDO\_TDI \\
                          &  &                           &                            & 3V3\_JTAG \\
                          &  &                           &                            & None \\
                          &  &                           &                            & None \\
                          &  &                           &                            & None \\
                          &  &                           &                            & None \\
                          &  &                           &                            & TCK \\
                          &  &                           &                            & None \\
                          &  &                           &                            & GND \\
                          &  &                           &                            & None \\
                          &  &                           &                            & None \\
                          &  &                           &                            & UART\_TX \\
                          &  &                           &                            & None \\
                          &  &                           &                            & UART\_RX \\
    \midrule
    \multicolumn{5}{r}{\textit{Continues on next page}} \\
    \pagebreak
    \midrule
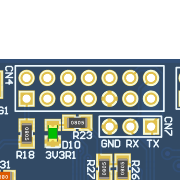
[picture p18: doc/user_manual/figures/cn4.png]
    \multirow{14}{*}{CN4} & \multirow{14}{*}{\raisebox{-\totalheight}{}} & \multirow{14}{*}{JTAG} & \multirow{14}{*}{Pin Header} & TDO\_TDI \\
                          &  &                           &                            & 3V3\_JTAG \\
                          &  &                           &                            & None \\
                          &  &                           &                            & None \\
                          &  &                           &                            & None \\
                          &  &                           &                            & None \\
                          &  &                           &                            & TCK \\
                          &  &                           &                            & None \\
                          &  &                           &                            & GND \\
                          &  &                           &                            & None \\
                          &  &                           &                            & None \\
                          &  &                           &                            & UART\_TX \\
                          &  &                           &                            & None \\
                          &  &                           &                            & UART\_RX \\
    \midrule
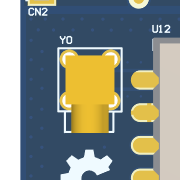
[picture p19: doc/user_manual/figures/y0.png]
    \multirow{10}{*}{Y0}  & \multirow{10}{*}{\raisebox{-\totalheight}{}} & \multirow{10}{*}{RF} & \multirow{10}{*}{MCX} &  \\
                          &  &                           &                            &  \\
                          &  &                           &                            &  \\
                          &  &                           &                            &  \\
                          &  &                           &                            & RF\_SIGNAL \\
                          &  &                           &                            & RF\_GND \\
                          &  &                           &                            &  \\
                          &  &                           &                            &  \\
                          &  &                           &                            &  \\
                          &  &                           &                            &  \\
    \midrule
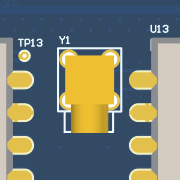
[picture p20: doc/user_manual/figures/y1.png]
    \multirow{10}{*}{Y1}  & \multirow{10}{*}{\raisebox{-\totalheight}{}} & \multirow{10}{*}{RF} & \multirow{10}{*}{MCX} &  \\
                          &  &                           &                            &  \\
                          &  &                           &                            &  \\
                          &  &                           &                            &  \\
                          &  &                           &                            & RF\_SIGNAL \\
                          &  &                           &                            & RF\_GND \\
                          &  &                           &                            &  \\
                          &  &                           &                            &  \\
                          &  &                           &                            &  \\
                          &  &                           &                            &  \\
    \bottomrule[1.5pt]
    \caption{Dedicated electrical interfaces.}
    \label{tab:icd}
\end{longtable}

\section{Mechanical interfaces}

The TTC 2.0 board has four mounting holes to fix the module into the CubeSat mechanical structure. These mounting holes are 3.2 mm in diameter and positioned on each corner of the PCB. These holes can be seen in Figures \ref{fig:ttc2-pcb-top} and \ref{fig:ttc2-pcb-bottom}.

\section{Printed Circuit Board}

This section presents some detailed information about the PCB of the TTC 2.0 module.

\subsection{Dimensions}

The TTC PCB dimensions follow the CubeSats industry standards, with a size of $89.15$ mm by $92.13$ mm \cite{nasa-handout}. The outline is specifically defined to improve the physical integration of modules and payloads into the mechanical structure. A drawing with the board dimensions is available in \autoref{fig:board-dimensions}.

\begin{figure}[!ht]
    \begin{center}
        
        \caption{Board dimensions for the TTC 2.0 module.}
        \label{fig:board-dimensions}
    \end{center}
\end{figure}

\subsection{Layout}

The TTC 2.0 module contains only two layers: top and bottom, as presented in Figures \ref{fig:ttc2-pcb-top} and \ref{fig:ttc2-pcb-bottom}. To design the layout, the Altium Designer\footnote{\href{https://www.altium.com/}{https://www.altium.com/}} software was used.

\begin{figure}[!ht]
    \begin{center}
        
        \caption{Top layer of the TTC 2.0 layout.}
        \label{fig:ttc2-layout-top}
    \end{center}
\end{figure}

\begin{figure}[!ht]
    \begin{center}
        
        \caption{Bottom layer of the TTC 2.0 layout.}
        \label{fig:ttc2-layout-bottom}
    \end{center}
\end{figure}

Simple PCBs with common manufacturing specifications were used to test and develop the module. These PCBs were defined as Engineering Models (EM). The Flight Model (FM, or the boards that can fly with the satellite) of the boards have the following manufacturing specifications:

\begin{itemize}
    \item \textbf{PCB specs.}: IPC 6012 Class 3
    \item \textbf{PCB thickness}: 1.6 mm
    \item \textbf{Material}: TG170 FR-4
    \item \textbf{Surface finish}: ENIG
    \item \textbf{Board finish}: Conformal coating application
\end{itemize}

\section{Peripherals}

The TTC 2.0 have some peripherals besides the microcontrollers, like sensors, watchdog timers, and radio modules. These peripherals are better described in this section.

\subsection{Power sensor}

The board has power sensors (model INA226AQDGSRQ1 from Texas Instruments) that use an I$^{2}$C interface to communicate with the microcontroller. There are four of these sensors in the module, one for each microcontroller and one for each radio module. It monitors voltage and current from a given bus through a shunt resistor (with a resistance of $0.1$ $\Omega$). The final measurement is continuous and made by an average of 128 measurements with an interval of 588 $\mu$s between each other.

\subsection{External watchdog timer}

Besides the internal watchdog of the microcontroller, there is also a redundant external one. For that, the TPS3823 IC from Texas Instruments is used. It has an integrated voltage monitor and a watchdog timer, with a timeout of 1600 ms. The boards have two of these ICs, one for each microcontroller.

\subsection{Radio module}

One of the main components of the board is the radio module (NiceRF RF4463F30), which uses an SPI interface to be controlled by the microcontroller. The radio has a dedicated power source of 5 V directly from the PC-104 bus. The output power of the RF signal generated by the radio is 30 dBm (1 W). The radio is half-duplex and has an integrated power amplifier and an RF switch, as shown in \autoref{fig:rf4463f30-block-diagram}.

\begin{figure}[!ht]
    \begin{center}
        
        \caption{Block diagram of the RF4463F30 module.}
        \label{fig:rf4463f30-block-diagram}
    \end{center}
\end{figure}

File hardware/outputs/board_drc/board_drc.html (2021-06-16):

Altium

# Design Rule Verification Report

Date: | | 6/15/2021
Time: | | 5:23:19 PM
Elapsed Time: | | 00:00:02
Filename: | | C:\Users\Yan Azeredo\Desktop\SpaceLab\ttc2\hardware\sources\board_layout.pcbdoc

Warnings: | | 0
Rule Violations: | | 0

## Summary

Warnings | Count
Total | 0

Rule Violations | Count
Clearance Constraint (Gap=0.254mm) (InNet('GND')),(All) | 0
Clearance Constraint (Gap=0.42mm) (InNet('RF_GND')),(InNet('RF_Transceiver_Main_Radio')) | 0
Clearance Constraint (Gap=0mm) (InNet('RF_GND')),(InNet('RF_GND')) | 0
Clearance Constraint (Gap=0.42mm) (InNet('RF_GND')),(All) | 0
Clearance Constraint (Gap=0.203mm) (All),(All) | 0
Clearance Constraint (Gap=0.42mm) (InNet('RF_GND')),(InNet('RF_Beacon_Radio')) | 0
Short-Circuit Constraint (Allowed=No) (All),(All) | 0
Un-Routed Net Constraint ( (All) ) | 0
Width Constraint (Min=0.508mm) (Max=0.508mm) (Preferred=0.508mm) (InNet('RA_0_VREF_MCU') and InNet('RA_1_VREF_MCU')) | 0
Width Constraint (Min=0.127mm) (Max=2.032mm) (Preferred=0.254mm) (All) | 0
Power Plane Connect Rule(Relief Connect )(Expansion=0.508mm) (Conductor Width=0.508mm) (Air Gap=0.254mm) (Entries=4) (All) | 0
Hole Size Constraint (Min=0.025mm) (Max=5.08mm) (All) | 0
Hole To Hole Clearance (Gap=0.254mm) (All),(All) | 0
Minimum Solder Mask Sliver (Gap=0mm) (All),(All) | 0
Silk To Solder Mask (Clearance=0mm) (IsPad),(All) | 0
Silk to Silk (Clearance=0.127mm) (All),(All) | 0
Net Antennae (Tolerance=0mm) (All) | 0
Height Constraint (Min=0mm) (Max=25.4mm) (Prefered=12.7mm) (All) | 0
Total | 0

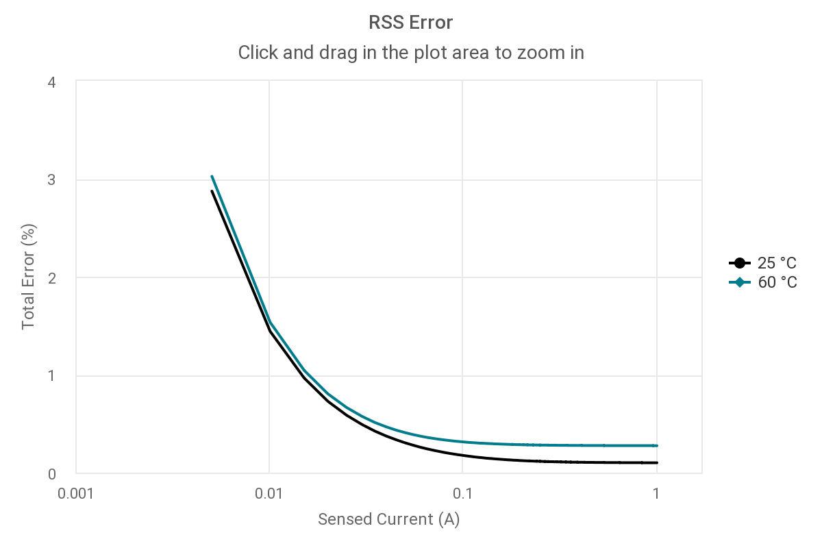
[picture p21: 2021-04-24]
hardware/images/ina226_100mohms_rss_error.png

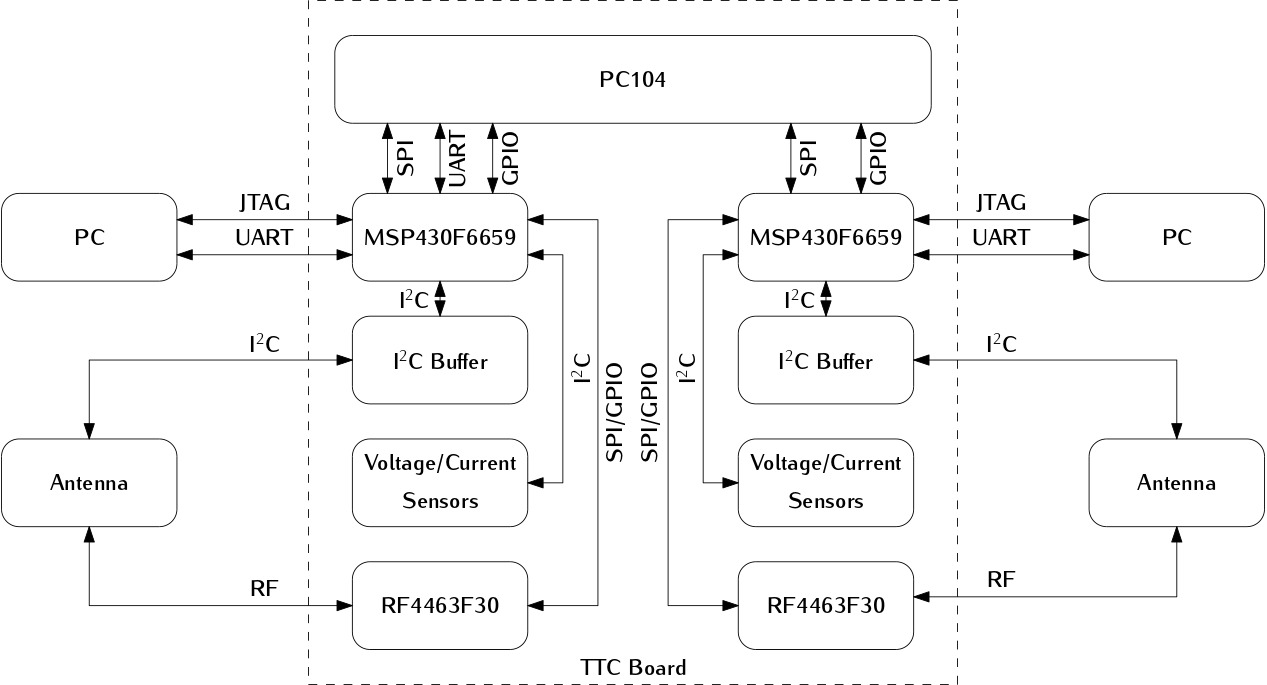
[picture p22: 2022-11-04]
doc/user_manual/figures/hardware-diagram.jpg

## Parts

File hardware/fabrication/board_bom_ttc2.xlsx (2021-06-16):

 |  |  | Bill of Materials
 |  |  | Source Data From: | ttc2_project.prjpcb
 |  |  | Project: | ttc2_project.prjpcb
 |  |  | Variant: | None
 |  |  | Project Code: | TTC2
 |  |  | Report Date: | 6/15/2021 | 5:35:21 PM
 |  |  | Print Date: | 2021-06-15 | 17:37:10
# | Designator | Quantity | Manufacturer | Manufacturer Part Number | Partnumber | Description | #Column Name Error:Package | Footprint | #Column Name Error:Mount | Fitted
1 | R7, R8, R9, R10, R11, R13, R14, R15, R16, R17, R24, R25, R26, R27, R28, R30, R31, R32, R33, R34 | 20 |  |  | CRCW080510K0FKEA | RES 10K OHM 1/8W 1% 0805 |  | 0805 |  | Fitted
2 | C8, C10, C12, C14, C16, C17, C19, C20, C37, C39, C41, C43, C45, C46, C48, C49 | 16 |  |  | CC0805KRX7R8BB104 | CAP CER 0.1UF 25V 10% X7R 0805 |  | CC0805 |  | Fitted
3 | J_P4, J_P5, J_P7, J_P8, J_P9, J_P10, J_P11, J_P12, J_P13, J_P14, J_V0, J_V1, J_V2, J_V3 | 14 |  |  | CRCW08050000Z0EA | RES 0R OHM 1/8W JUMPER 0805 |  | 0805 |  | Fitted
4 | C7, C9, C11, C13, C15, C18, C36, C38, C40, C42, C44, C47 | 12 |  |  | TPSP106M010R2000 | CAP Tantalum 10uF 10V 20% 0805 |  | CC0805_Tantalum |  | Fitted
5 | R2, R3, R4, R5, R6, R19, R20, R21, R22, R23 | 10 |  |  | RC0805FR-071KL | RES 1.0K OHM 1/8W 1% 0805 |  | 0805 |  | Fitted
6 | R1, R18, V1, V2, V3, V4 | 6 |  |  | RC0805FR-0747KL | RES 47k OHM 1/8W 1% 0805 |  | 0805 |  | Fitted
7 | RS1, RS2, RS3, RS4 | 4 |  |  | SR732ATTER100F | RES 0.1R OHM 1/3W 1% 0805 |  | 0805 |  | Fitted
8 | C2, C3, C31, C32 | 4 |  |  | 08051A100FAT2A | CAP CER 10pF 100V 0805 |  | CC0805 |  | Fitted
9 | C4, C5, C33, C34 | 4 |  |  | CL21C120FBANNNC | CAP CER 12pF 50V 0805 |  | CC0805 |  | Fitted
10 | CN1, CN2, CN5, CN6 | 4 |  |  | 0532610671 | PicoBlade 6 Position Right Angle Connector Header Surface Mount 0.049" (1.25mm) |  | PICOBLADE 6PIN Right Angle |  | Fitted
11 | U4, U5, U9, U10 | 4 | Texas Instruments |  | INA226AQDGSRQ1 | High-Side Measurement, Bi-Directional Current/Power Monitor w/I2C Interface |  | DGS10 |  | Fitted
12 | D1, D2, D3, D4 | 4 |  |  | LTST-C170KFKT | LED Orange SMD - Orange 605nm LED Indication - Discrete 2V 0805 (2012 Metric) |  | 0805-ORANGE-LED |  | Fitted
13 | D6, D7, D8, D9 | 4 |  |  | LTST-C170KRKT | LED Red SMD - Red 631nm LED Indication, Discrete 2V 0805 (2012 Metric) |  | 0805-RED-LED |  | Fitted
14 | C21, C50 | 2 |  |  | CL21B103KAANNNC | CAP CER 0.01uF 25V 10% X7R 0805 |  | CC0805 |  | Fitted
15 | C1, C30 | 2 |  |  | C0805C474K5RACTU | CAP CER 0.47UF 50V 10% X7R 0805 |  | CC0805 |  | Fitted
16 | C6, C35 | 2 |  |  | C0603X102J4RECAUTO | CAP CER 1nF 16V 0603 5% |  | CC0603 |  | Fitted
17 | CN7, CN8 | 2 | TE Connectivity AMP | 4-103327-5 | 4-103327-5 | Connector Header Through Hole 3 position 0.100" (2.54mm) |  | HDR 1X3 |  | Fitted
18 | Y2, Y4 | 2 |  |  | ABM8X-102-32.000MHZ-T | 32MHz ±10ppm Crystal 10pF 60 Ohm -40°C ~ 125°C |  | XTAL_ABM8X |  | Fitted
19 | Y0, Y1 | 2 |  |  | 133-3701-311 | MCX Connector Jack, Female Socket 50Ohm Through Hole, Right Angle Solder |  | CONN MCX JACK R/A 50 OHM SMD |  | Fitted
20 | Y3, Y5 | 2 |  |  | ECS-.327-12.5-34S-TR | 32.768kHz ±20ppm Crystal 12.5pF 70 kOhm -40°C ~ 125°C |  | ABS06 0805 |  | Fitted
21 | D5, D10 | 2 |  |  | LTST-C171GKT | LED Green SMD - Green 569nm LED Indication - Discrete 2.1V 0805 (2012 Metric) |  | 0805-GREEN-LED |  | Fitted
22 | CN3, CN4 | 2 | Harwin | M20-9980745 | M20-9980745 | Connector Header Through Hole 14 position 0.100" (2.54mm) |  | CONN HEADER VERT 14POS 2.54MM |  | Fitted
23 | U2, U7 | 2 | Texas Instruments |  | MSP430F6659IPZR | CPUXV2 series Microcontroller IC 16-Bit 20MHz 512KB (512K x 8) FLASH 100-LQFP (14x14) |  | LQFP-100 |  | Fitted
24 | U12, U13 | 2 |  |  | RF4463F30 | RF4463F30 High Power Wireless Transceiver Module |  | RF4463F30 |  | Fitted
25 | U6, U11 | 2 |  |  | TCA4311ADR | IC SIGNAL BUFFER I2C 8SOIC HOTSWAP |  | SOIC8 |  | Fitted
26 | U3, U8 | 2 | Texas Instruments |  | TPS3823-33QDBVRQ1 | Processor Supervisory Circuit, 1 Supply Monitored, -40 to 85 degC, 5-Pin SOT-23 (DBV), Green (RoHS & no Sb/Br) |  | DBV0005A_N |  | Fitted
27 | ESD | 1 |  |  | RMCF0805FG1M00 | RES 1000K OHM 1/8W 1% 0805 |  | 0805 |  | Fitted
28 | FB1 | 1 |  |  | BLM21PG300SN1D | Ferrite Bead 30 OHM 4A 100MHz |  | IND0805 |  | Fitted
29 | CN9 | 1 |  |  | 826646-2 | Connector Header Through Hole 2 position 0.100" (2.54mm) |  | HDR 1X2 |  | Fitted
30 | PC104 | 2 |  |  | SSW-126-04-G-D | Connector Header Through Hole 52 position 0.100" (2.54mm) - PC104 used in the TTC module |  | PC104_TTC |  | Fitted

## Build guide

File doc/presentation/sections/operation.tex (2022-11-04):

%
% operation.tex
%
% Copyright (C) 2022 by SpaceLab.
%
% TTC 2.0 Critical Design Review
%
% This work is licensed under the Creative Commons Attribution-ShareAlike 4.0
% International License. To view a copy of this license,
% visit http://creativecommons.org/licenses/by-sa/4.0/.
%

%
% \brief Project management slides.
%
% \author Gabriel Mariano Marcelino <gabriel.mm8@gmail.com>
% \author Miguel Boing <miguelboing13@gmail.com>
%
% \version 0.1.0
%
% \date 2022/08/18
%

\begin{frame}{Operation}

    \begin{itemize}
        \item By default, the TTC will always operate in RX mode
        \vspace{0.3cm}
        \item If requested by an external device, a packet is transmitted (TX mode)
        \vspace{0.3cm}
        \item An external device can read or write from/to the internal parameters
        \vspace{0.3cm}
        \item The received packets are stored in a queue with five positions (up to five packets can be stored)
        \vspace{0.3cm}
        \item When requested, an external device can read the decoded packets from the queue
    \end{itemize}

\end{frame}

\begin{frame}{RF Protocol: \href{https://mgm8.github.io/pyngham/protocol.html}{\textcolor{cyan}{\underline{NGHam}}}}

    \begin{itemize}
        \item With FEC (Reed-Solomon with seven different schemes)
        \item Up to 220 bytes of data per packet
    \end{itemize}

    \begin{figure}[!ht]
        \begin{center}
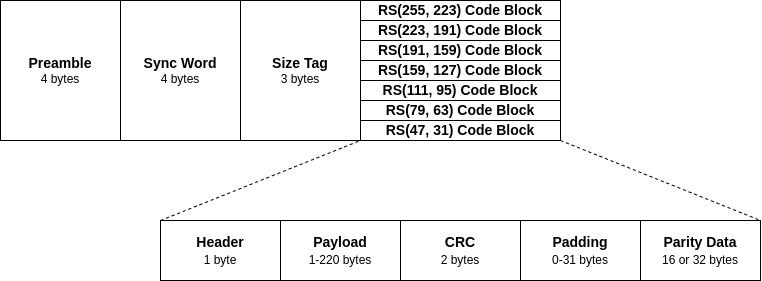
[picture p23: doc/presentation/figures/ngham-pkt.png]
            
        \end{center}
    \end{figure}

\end{frame}

\begin{frame}{NGHam: Sizes}

    \begin{table}[!htb]\small
    \centering
    \label{tab:ngham-sizes}
    \begin{tabular}{cccC{1.3cm}C{1.8cm}}
        \toprule[1.5pt]
        \textbf{Size Num.} & \textbf{Tag} & \textbf{RS Config.} & \textbf{Parity Bytes} & \textbf{Max. Data Bytes} \\
        \midrule
        1 & 59, 73, 205   & RS(47, 31)   & 16 & 28 \\
        2 & 77, 218, 87   & RS(79, 63)   & 16 & 60 \\
        3 & 118, 147, 154 & RS(111, 95)  & 16 & 92 \\
        4 & 155, 180, 174 & RS(159, 127) & 32 & 124 \\
        5 & 160, 253, 99  & RS(191, 159) & 32 & 156 \\
        6 & 214, 110, 249 & RS(223, 191) & 32 & 188 \\
        7 & 237, 39, 52   & RS(255, 223) & 32 & 220 \\
        \bottomrule[1.5pt]
    \end{tabular}

\end{table}

\end{frame}

\begin{frame}{NGHam: Parameters}

    \begin{itemize}
        \item \textbf{Preamble}: 4 $\times$ 0xAA
        \item \textbf{Sync. Word}: 0x5D, 0xE6, 0x2A, 0x7E
        \item \textbf{CRC}:
        \begin{itemize}
            \item \textit{Polynomial}: 0x1021
            \item \textit{Initial value}: 0xFFFF
            \item \textit{Final XOR value}: 0xFFFF
        \end{itemize}
        \item \textbf{Reed-Solomon}:
        \begin{itemize}
            \item \textit{Symbol size}: 8
            \item \textit{GF polynomial}: 0x187 (coeficients form)
            \item \textit{First root of RS code generator polynomial}: 112 (index form)
            \item \textit{Primitive element}: 11
            \item \textit{Number of roots}: 16 or 32
        \end{itemize}
    \end{itemize}

\end{frame}

\begin{frame}{NGHam: Scrambling}
    
    \begin{itemize}
        \item Before transmitting a packet, the RS code block is scrambled by making a byte xor operation with a pre-generated table based on the polynomial $x^{8} + x^{7} + x^{5} + x^{3} + 1$ (defined in the CCSDS 131.0-B-3 standard)
        \vspace{0.5cm}
        \item When the receiver receives a packet, it also perform the same operation to de-scramble the RS code block and get the original content of the RS part of the packet
        \vspace{0.5cm}
        \item More information: \href{https://public.ccsds.org/Pubs/132x0b3.pdf}{\textcolor{blue}{\underline{CCSDS 131.0-B-3}}} (section 8.3)
    \end{itemize}

\end{frame}

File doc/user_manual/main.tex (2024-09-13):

%
% main.tex
%
% Copyright The TTC 2.0 Contributors.
%
% TTC 2.0 Documentation
%
% This work is licensed under the Creative Commons Attribution-ShareAlike 4.0
% International License. To view a copy of this license,
% visit http://creativecommons.org/licenses/by-sa/4.0/.
%

%
% \brief Main file.
%
% \author Gabriel Mariano Marcelino <gabriel.mm8@gmail.com>
%
% \version 1.0.0
%
% \date 2021/04/01
%

\documentclass[a4paper,12pt]{book}

\usepackage{spacelab_book}

\title{TTC 2.0 Documentation}
\author{SpaceLab}
\date{\today}

% File metadata
\hypersetup
{
    pdfauthor   = {SpaceLab},
    pdfsubject  = {\thetitle},
    pdftitle    = {\thetitle},
    pdfkeywords = {Nanosatellites, CubeSats, TTC}
}

\begin{document}

    \pagenumbering{roman}
    \setcounter{page}{1}

    \input{header/titlepage}
    \cleardoublepage
    \input{header/authorpage}
    \cleardoublepage

    \listoffigures
    \addcontentsline{toc}{chapter}{List of Figures}

    \listoftables
    \addcontentsline{toc}{chapter}{List of Tables}

%----------- Nomenclature List ---------------
\nomenclature{\textbf{PCB}}{\textit{Printed Circuit Board.}}
\nomenclature{\textbf{GOLDS}}{\textit{Global Open coLlecting Data System.}}
\nomenclature{\textbf{UFSC}}{\textit{Universidade Federal de Santa Catarina.}}
\nomenclature{\textbf{RAM}}{\textit{Random Access Memory.}}
\nomenclature{\textbf{RF}}{\textit{Radio Frequency.}}
\nomenclature{\textbf{SRAM}}{\textit{Static Random Access Memory.}}
\nomenclature{\textbf{GFSK}}{\textit{Gaussian Frequency Shift Keying.}}
\nomenclature{\textbf{GMSK}}{\textit{Gaussian Minimum Shift Keying.}}
\nomenclature{\textbf{NGHam}}{\textit{Next Generation Ham Radio.}}
\nomenclature{\textbf{UART}}{\textit{Universal Asynchronous Receiver / Transmitter.}}
\nomenclature{\textbf{SPI}}{\textit{Serial Peripheral Interface.}}
\nomenclature{\textbf{HAL}}{\textit{Hardware Abstraction Layer.}}
\nomenclature{\textbf{I$^2$C}}{\textit{Inter-Integrated Circuit.}}
\nomenclature{\textbf{RTOS}}{\textit{Real Time Operating System.}}
\nomenclature{\textbf{OBDH}}{\textit{On-Board Data Handling.}}
\nomenclature{\textbf{EPS}}{\textit{Electric Power System.}}
\nomenclature{\textbf{uC}}{\textit{MicroController.}}
\nomenclature{\textbf{FEC}}{\textit{Forward Error Correction.}}
\nomenclature{\textbf{RS}}{\textit{Reed-Solomon.}}
\nomenclature{\textbf{JTAG}}{\textit{Joint Test Action Group.}}
\nomenclature{\textbf{SDR}}{\textit{Software-Defined Radio.}}
\nomenclature{\textbf{EM}}{\textit{Engineering Model.}}
\nomenclature{\textbf{FM}}{\textit{Flight Model.}}
\nomenclature{\textbf{TTC}}{\textit{Telemetry, Tracking and Command.}}
%-----------------------------------------

    \printnomenclature
    \addcontentsline{toc}{chapter}{Nomenclature}

    \tableofcontents
    \cleardoublepage
    
    \pagenumbering{arabic}
    \setcounter{page}{1}

    \input{chapters/introduction}
    \input{chapters/hardware}
    \input{chapters/firmware}
    \input{chapters/operation}
    \input{chapters/assembly}
    \input{chapters/references}
%    \input{appendices/appendices}

\end{document}

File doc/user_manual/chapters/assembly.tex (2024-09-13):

%
% assembly.tex
%
% Copyright The TTC 2.0 Contributors.
%
% TTC 2.0 Documentation
%
% This work is licensed under the Creative Commons Attribution-ShareAlike 4.0
% International License. To view a copy of this license,
% visit http://creativecommons.org/licenses/by-sa/4.0/.
%

%
% \brief Assembly instructions chapter.
%
% \author Gabriel Mariano Marcelino <gabriel.mm8@gmail.com>
%
% \version 1.0.0
%
% \date 2021/01/16
%

\chapter{Assembly instructions} \label{ch:assembly}

This chapter will describe how to customize the radio configuration, power-on the board, import and flash the source code and finally alternatives to encode/decode to be transmitted/received packages from the TTC 2.0 module.

\section{Radio configuration} \label{sec:wds}

This section is a tutorial designed to generate a source code file with basic configuration parameters for the radio module. To achieve this, the WDS software from Silicon Labs (version 3.2.11.0), which is only available on Windows, will be used.

\subsection{Steps}

After the installation of the software, the procedures to configure the beacon radio are described bellow.

\subsubsection{Step 1}

\begin{enumerate}
    \item Open the WDS software.
    \item The following box will appear in the center of the window.
    \item Click in "Simulate radio" and go to the next step.
\end{enumerate}

\begin{figure}[!h]
	\begin{center}
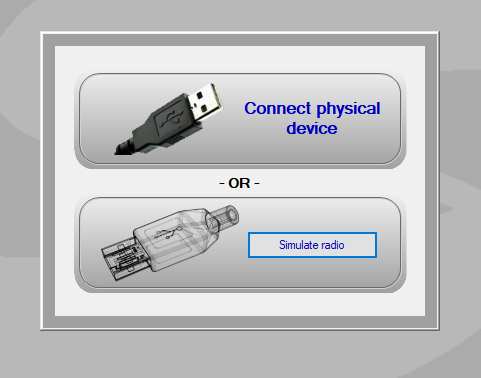
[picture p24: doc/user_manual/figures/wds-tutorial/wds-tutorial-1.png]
		
		\caption{Step 1 of the radio configuration.}
		\label{fig:wds-tutorial-step-1}
	\end{center}
\end{figure}

\subsubsection{Step 2}

\begin{enumerate}
    \item In the list of radios that appeared on the new window, select the chip type ``Si4463''.
    \item In the revision column, select ``B1''.
    \item Click on ``Select Radio" to go to the next step.
\end{enumerate}

\begin{figure}[!h]
	\begin{center}
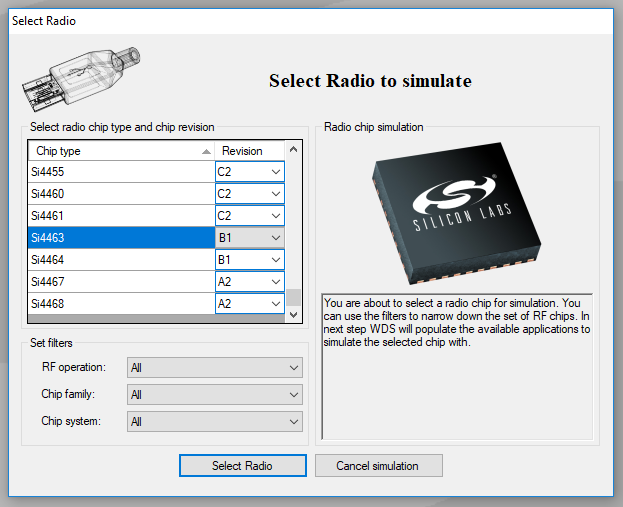
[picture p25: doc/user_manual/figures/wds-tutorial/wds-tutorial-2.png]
		
		\caption{Step 2 of the radio configuration.}
		\label{fig:wds-tutorial-step-2}
	\end{center}
\end{figure}

\subsubsection{Step 3}

\begin{enumerate}
    \item Select ``Radio Configuration Application''.
    \item Click on ``Select Application'' to go to the next step.
\end{enumerate}

\begin{figure}[!h]
	\begin{center}
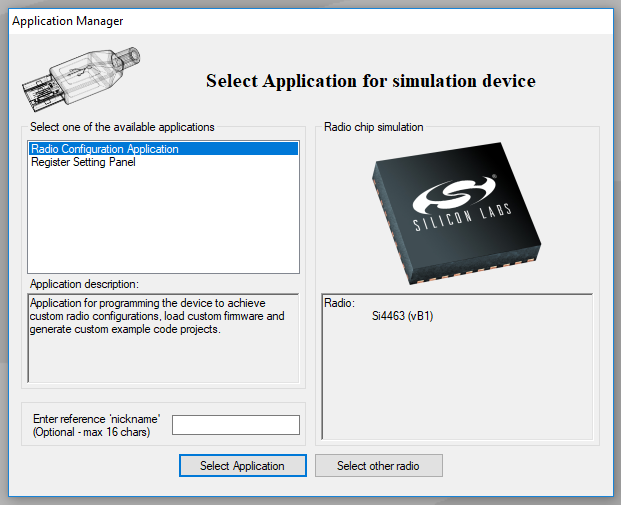
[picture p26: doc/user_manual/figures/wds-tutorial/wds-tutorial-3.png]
		
		\caption{Step 3 of the radio configuration.}
		\label{fig:wds-tutorial-step-3}
	\end{center}
\end{figure}

\subsubsection{Step 4}

\begin{enumerate}
    \item In the ``Frequency and power'' tab, change the base frequency to 145.9 MHz.
    \item Change the channel spacing to 0 kHz.
    \item Change the crystal tolerance to 10.0 ppm (Both RX and TX).
    \item Go to the next step.
\end{enumerate}

\begin{figure}[!h]
	\begin{center}
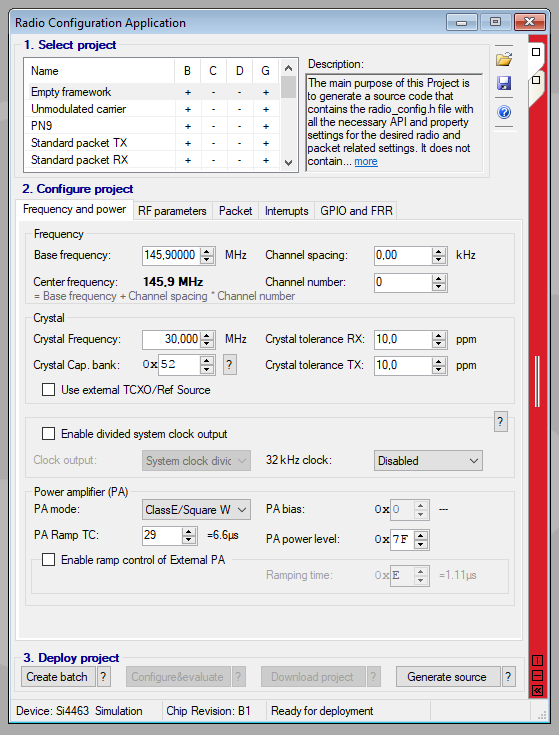
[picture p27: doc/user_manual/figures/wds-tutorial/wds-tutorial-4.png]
		
		\caption{Step 4 of the radio configuration.}
		\label{fig:wds-tutorial-step-4}
	\end{center}
\end{figure}

\subsubsection{Step 5}

\begin{enumerate}
    \item In the ``RF parameters" tab, change the modulation type to ``2GFSK''.
    \item Change the the data rate to 1.2 kbps.
    \item Change the deviation to 2.5 kHz.
    \item Go to the next step.
\end{enumerate}

\begin{figure}[!h]
	\begin{center}
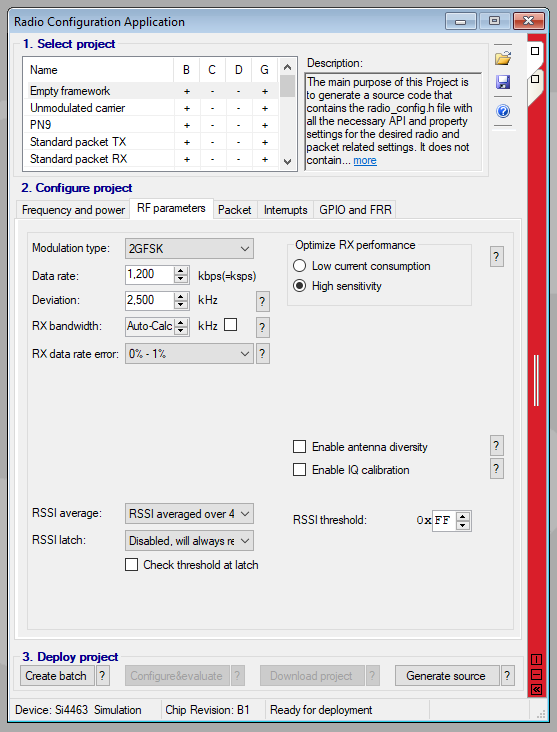
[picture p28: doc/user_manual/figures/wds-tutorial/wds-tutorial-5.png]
		
		\caption{Step 5 of the radio configuration.}
		\label{fig:wds-tutorial-step-5}
	\end{center}
\end{figure}

\subsubsection{Step 6}

\begin{enumerate}
    \item In the ``Packet'' tab, many subtabs will appear. In ``Preamble" change the ``Preamble TX length'' to 4 bytes.
    \item Again, in ``Preamble'', change the ``Preamble pattern'' to ``Std. 1010 pattern (>= 32 and < 40 bits)''.
    \item Go to the next step.
\end{enumerate}

\begin{figure}[!h]
	\begin{center}
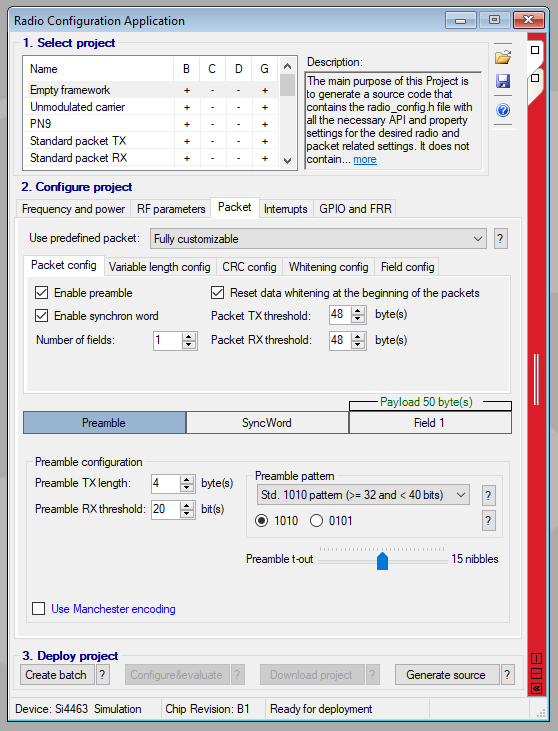
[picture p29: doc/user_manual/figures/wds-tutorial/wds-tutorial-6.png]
		
		\caption{Step 6 of the radio configuration.}
		\label{fig:wds-tutorial-step-6}
	\end{center}
\end{figure}

\subsubsection{Step 7}

\begin{enumerate}
    \item In the ``Sync Word'' tab, change the sync word length field to ``4 bytes''.
    \item In the ``Sync Word (on air int.)'', enter the following sequence: 5D E6 2A 7E. This sequence is the sync word used by the NGHam protocol.
    \item Go to the next step.
\end{enumerate}

\begin{figure}[!h]
	\begin{center}
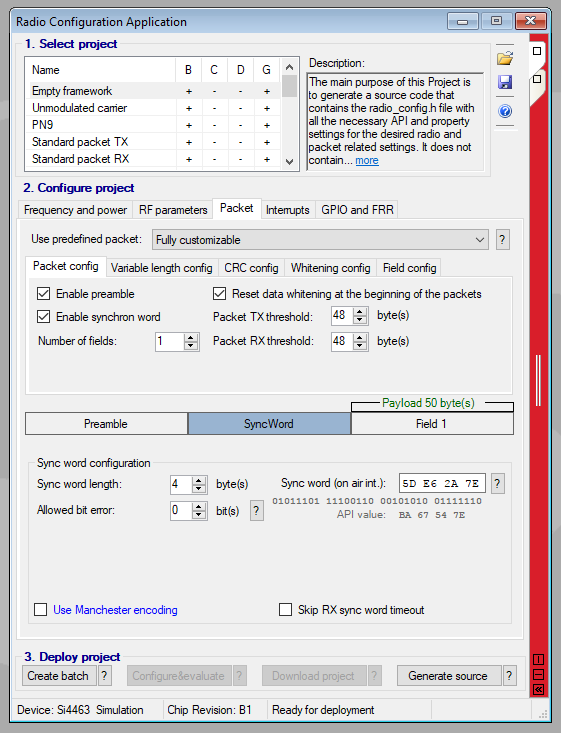
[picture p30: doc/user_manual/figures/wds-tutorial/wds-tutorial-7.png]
		
		\caption{Step 7 of the radio configuration.}
		\label{fig:wds-tutorial-step-7}
	\end{center}
\end{figure}

\subsubsection{Step 8}

\begin{enumerate}
    \item In the ``Field 1'' tab, change the ``Field length'' to 50 bytes.
    \item Go to the next step.
\end{enumerate}

\begin{figure}[!h]
	\begin{center}
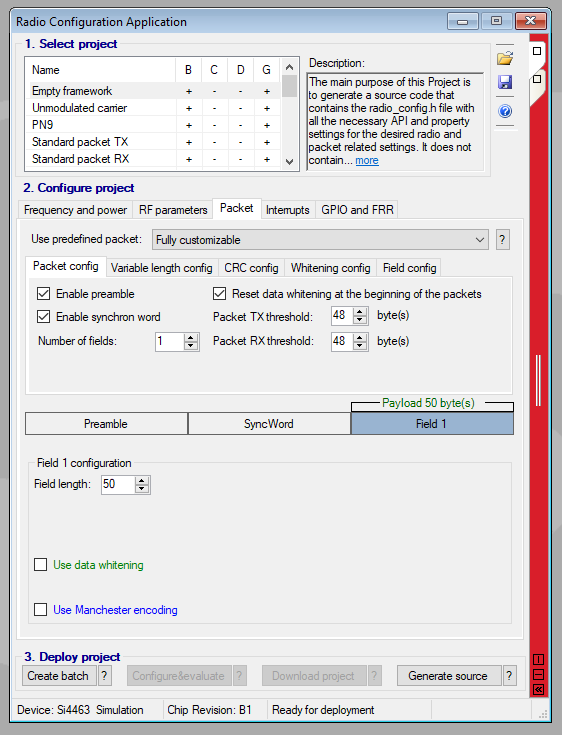
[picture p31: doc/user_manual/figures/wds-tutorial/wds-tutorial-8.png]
		
		\caption{Step 8 of the radio configuration.}
		\label{fig:wds-tutorial-step-8}
	\end{center}
\end{figure}

\subsubsection{Step 9}

\begin{enumerate}
    \item In the ``Variable length config'' tab, there is no values to change.
    \item Go to the next step.
\end{enumerate}

\begin{figure}[!h]
	\begin{center}
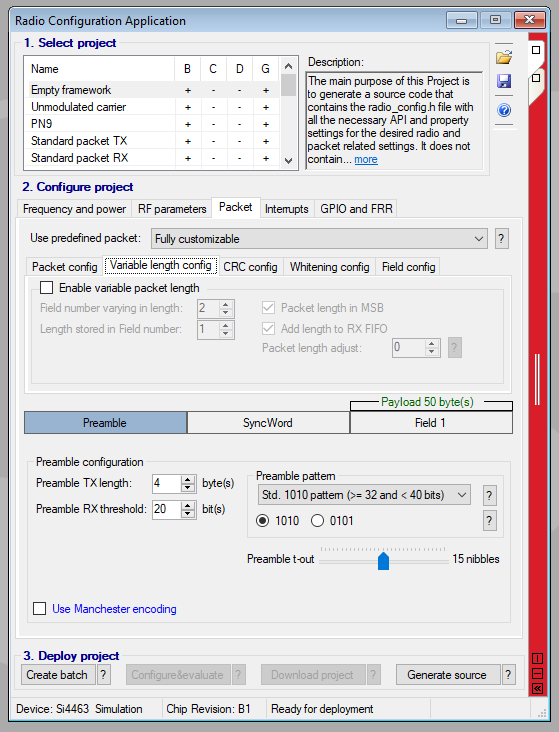
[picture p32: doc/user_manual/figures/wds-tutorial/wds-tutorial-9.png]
		
		\caption{Step 9 of the radio configuration.}
		\label{fig:wds-tutorial-step-9}
	\end{center}
\end{figure}

\subsubsection{Step 10}

\begin{enumerate}
    \item In the ``CRC config'' tab, choose ``No CRC.'' in ``CRC polynomial''.
    \item Go to the next step.
\end{enumerate}

\begin{figure}[!h]
	\begin{center}
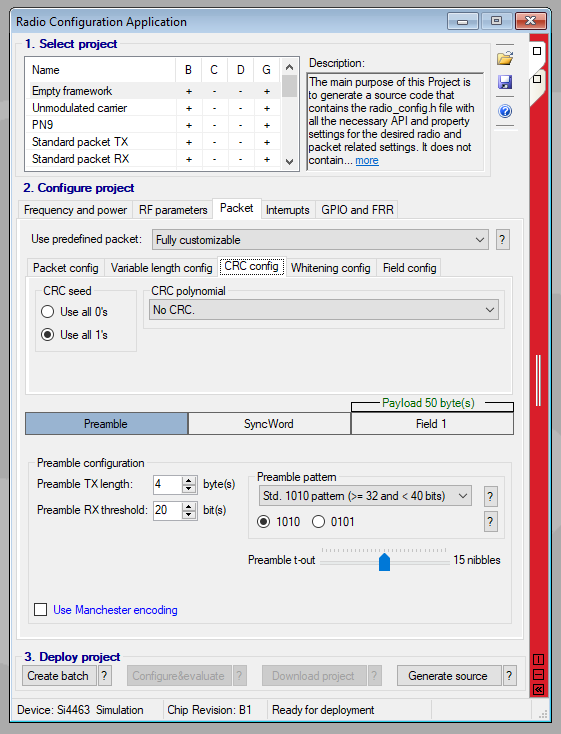
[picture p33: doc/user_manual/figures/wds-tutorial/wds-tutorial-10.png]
		
		\caption{Step 10 of the radio configuration.}
		\label{fig:wds-tutorial-step-10}
	\end{center}
\end{figure}

\subsubsection{Step 11}

\begin{enumerate}
    \item In the ``Whitening config'' tab, there is no values to change.
    \item Go to the next step.
\end{enumerate}

\begin{figure}[!h]
	\begin{center}
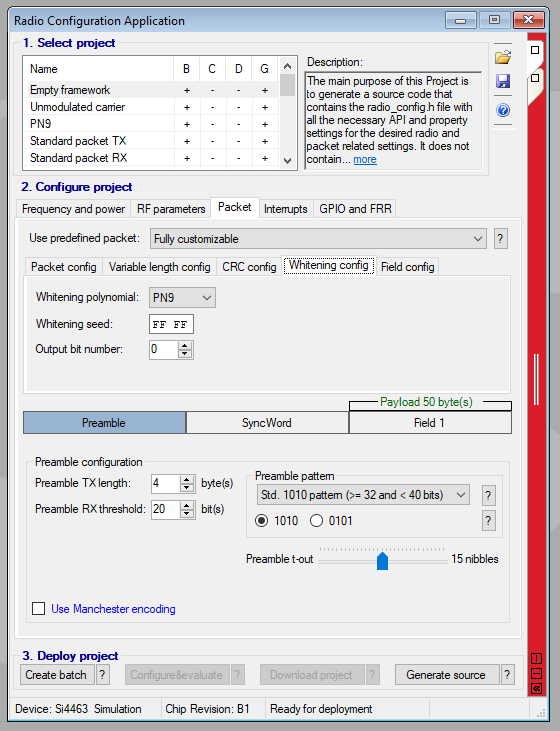
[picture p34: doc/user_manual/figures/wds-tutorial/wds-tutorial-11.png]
		
		\caption{Step 11 of the radio configuration.}
		\label{fig:wds-tutorial-step-11}
	\end{center}
\end{figure}

\subsubsection{Step 12}

\begin{enumerate}
    \item In the ``Field config'' tab, there is no values to change.
    \item Go to the next step.
\end{enumerate}

\begin{figure}[!h]
	\begin{center}
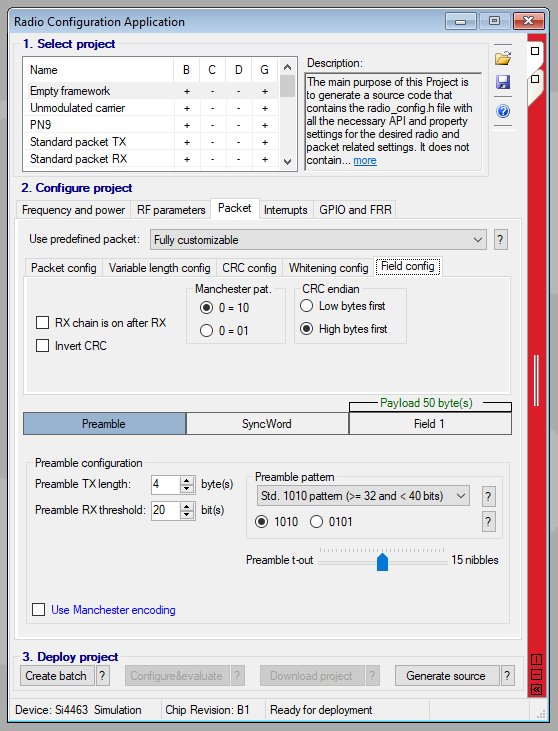
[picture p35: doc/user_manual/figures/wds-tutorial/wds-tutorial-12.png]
		
		\caption{Step 12 of the radio configuration.}
		\label{fig:wds-tutorial-step-12}
	\end{center}
\end{figure}

\subsubsection{Step 13}

\begin{enumerate}
    \item In the ``Interrupts'' tab, there is no values to change.
    \item Go to the next step.
\end{enumerate}

\begin{figure}[!h]
	\begin{center}
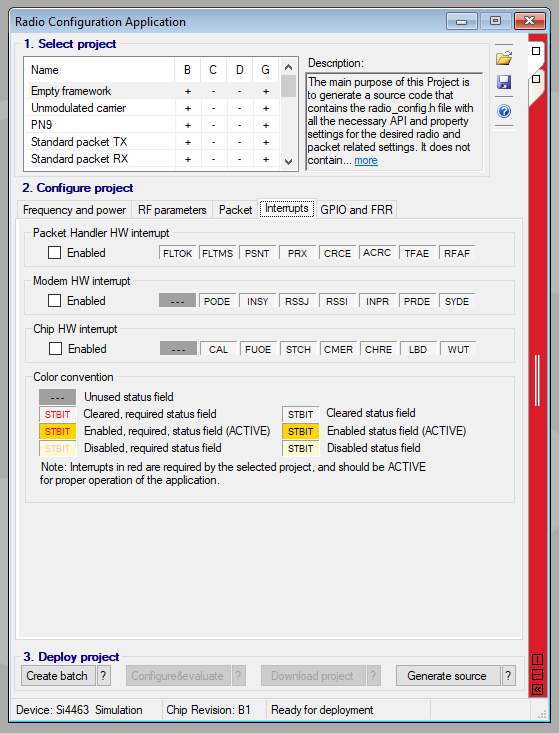
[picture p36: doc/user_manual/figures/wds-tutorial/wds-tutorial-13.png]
		
		\caption{Step 13 of the radio configuration.}
		\label{fig:wds-tutorial-step-13}
	\end{center}
\end{figure}

\subsubsection{Step 14}

\begin{enumerate}
    \item In the ``GPIO and FRR'' tab, enable pullup in GPIO1 and choose ``TX\_FIFO\_EMPTY - This output is...'' as functionality.
    \item Enable pullup in GPIO2 and choose ``RX\_STATE - This output is...'' as functionality.
    \item Enable pullup in GPIO3 and choose ``TX\_STATE - This output is...'' as functionality.
    \item Enable pullup in NIRQ and choose ``Active low interrupt signal'' as functionality.
    \item Enable pullup in SDO and choose ``SDO - Output SPI Serial data out.'' as functionality.
    \item Select ``Global status'' for the ``Fast Response Register A''.
    \item Select ``Global interrupt pending'' for the ``Fast Response Register B''.
    \item Select ``Packet Handler status'' for the ``Fast Response Register C''.
    \item Select ``Chip status'' for the ``Fast Response Register D''.
    \item Go to the next step.
\end{enumerate}

\begin{figure}[!h]
	\begin{center}
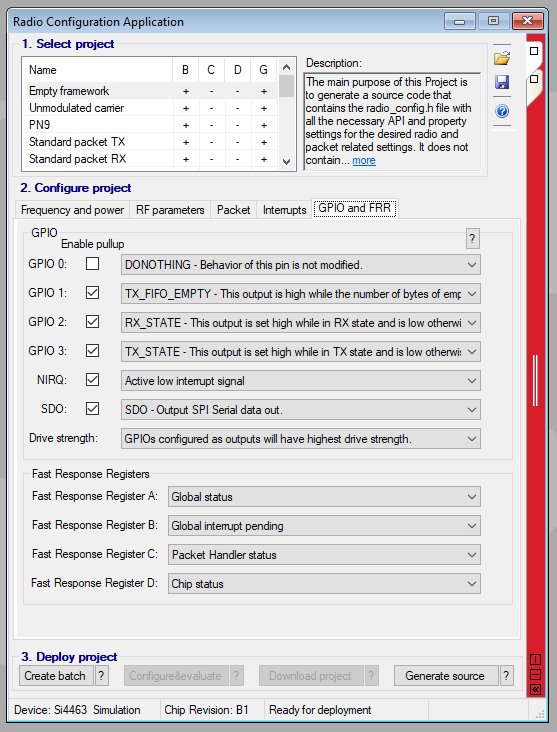
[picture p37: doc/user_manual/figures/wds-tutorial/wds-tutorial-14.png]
		
		\caption{Step 14 of the radio configuration.}
		\label{fig:wds-tutorial-step-14}
	\end{center}
\end{figure}

\subsubsection{Step 15}

\begin{enumerate}
    \item Click in ``Generate Source'' and select the ``.h'' type of source.
    \item The software will ask where to save the generated file.
    \item The generated *.h file must be copied to the directory of the rf4463 driver.
\end{enumerate}

\subsection{Final remarks}

This tutorial has the objective of generate a basic configuration parameters of the radio, some functionalities of the radio are not covered by the WDS software, and so, must be configured/controlled in the device driver.

\section{Powering the module}

The TTC 2.0 has three power supply inputs: one 3V3 supply to power the MCU and all the external components, two 5 V inputs to power the transceivers.

The 3V3 input voltage rail is accessible at the PC-104 H2-27 and H2-28 pins. You can also supply the 3V3 rail with MSP-FET JTAG connector by connecting the jumper CN9. This last option should only be used for debug as it requires the MSP-430 FET to be connected.

The transceiver supply rails are only accessible on the PC-104: H1-49 and H1-50 for radio 0 and H1-51 and H1-52 for radio 1. 

The TTC 2.0 module has only one common ground and it can be accessed by multiple pins on the PC-104 (see \autoref {tab:pc104-signals})

It is recommended, for safety reasons, to use different supply channels for each supply rail. Also, for extra safety it is recommended to add current cut-off limits: use 30 mA for the 3V3 and 500 mA for the radio 5 V power rails. 

\section{Compiling, building and flashing the source code}

This tutorial is a reference to compile, build and flash the firmware of the TTC 2.0 module using the Texas Instruments IDE: Code Composer Studio (CCS) version 12.

%All the software development was made using the Code Composer Studio (CCS) IDE, version 12. To load the code into the TTC 2.0 MCU, the MSP-FET can be used.

\subsection{Importing the source code in the CCS IDE}

The TTC 2.0 releases are available to download at the TTC 2.0 Github releases page \cite{ttc2-releases}. The CCS IDE is available at the Texas Instruments website \cite{ccs-studio}.

The steps bellow describe how to import the source code in the CCS IDE:

\begin{enumerate}
    \item Extract the ttc2-x.x.zip file.  
    \item Open the CCS IDE.
    \item Go to ``Project'' -> ``Import CCS Projects...''.
    \item The window from the figure \ref{fig:compiling-tutorial} will appear on the screen.
    \item On ``Select search-directory:'' select ``\textit{project\_path/ttc2-x.x/firmware}''.
    \item Click on ``Finish''.
    
    \item After importing the project, select the project on the ``Project Explorer'' and open the ``Properties'' tab (you can use the shortcut \textit{Alt+Enter} or right-click on the project's name). 
    \item The window from the \autoref{fig:project_properties} will appear on the screen.
    \item On ``Variant'', select the MCU partnumber (MSP430F6659 or MSP430F5659).
    \item On ``Compiler Version'', select ``TI v21.6.1.LTS'' or higher.
    \item Click on ``Apply and Close''.
\end{enumerate}

\begin{figure}[!h]
	\begin{center}
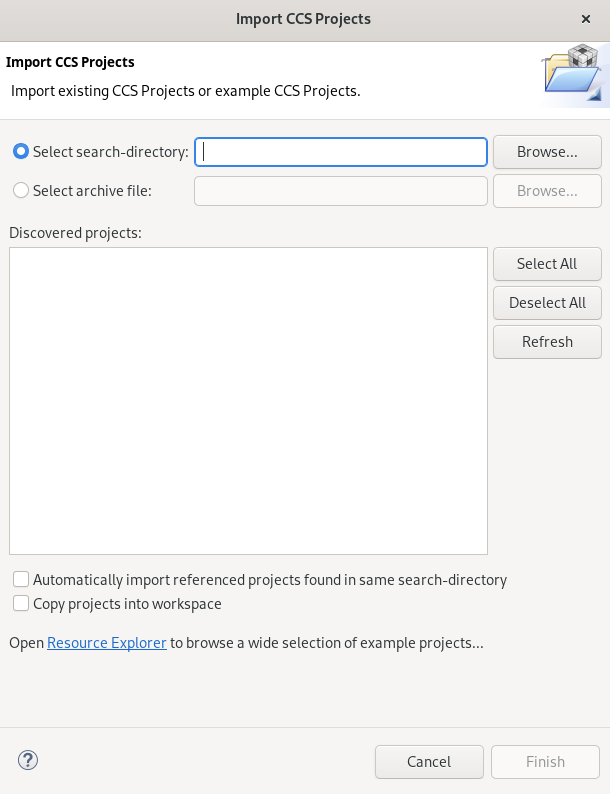
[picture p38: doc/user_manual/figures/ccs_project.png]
		
		\caption{New CCS project window.}
		\label{fig:compiling-tutorial}
	\end{center}
\end{figure}

\begin{figure}[!h]
	\begin{center}
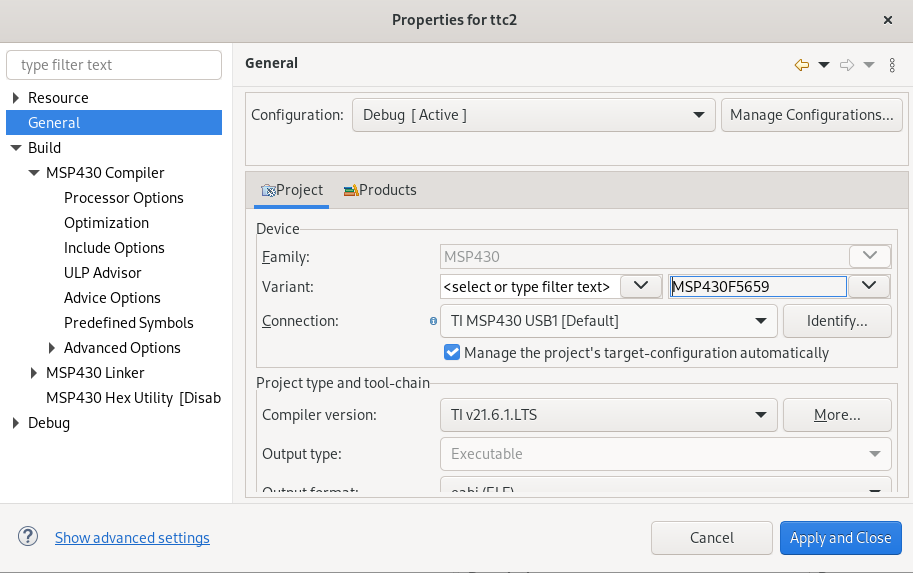
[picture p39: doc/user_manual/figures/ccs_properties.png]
		
		\caption{CCS project's properties window.}
		\label{fig:project_properties}
	\end{center}
\end{figure}

\subsection{Customize the project}

Since the TTC 2.0 has two MCU modules it is needed to specific which one you want to target. Access the configuration header file on the ``Project Explorer" at ``\textit{config/config.h}'', change the ``RADIO\_MODULE'' macro between '0' or '1' (The module '1' is the one closest to the PC-104).

Each MCU module controls a corresponding transceiver, to customize the transceiver configuration (as shown on \autoref{sec:wds}) copy all the code on the header file generated by the WDS software and paste it at the ``config/radio\_x\_config.h''.

\subsection{Compiling and building}

To compile and build the firmware, click on ``Project'' -> ``Build Project''.

\subsection{Flashing}

With the board turned on and the MSP-FET connected, click on ``Run'' -> ``Load''. If no errors occur, the firmware was loaded successfully to the board.

\section{Receiving and sending telecommands}

The structure of the telecommands are described at \autoref{ch:operation}. The standard solution to implement a ground-station is using the SpaceLab transmitter and decoder solutions \cite{sl-transmitter} \cite{sl-decoder} combined with and RTL-SDR.

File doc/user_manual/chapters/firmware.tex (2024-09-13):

%
% firmware.tex
%
% Copyright The TTC 2.0 Contributors.
%
% TTC 2.0 Documentation
%
% This work is licensed under the Creative Commons Attribution-ShareAlike 4.0
% International License. To view a copy of this license,
% visit http://creativecommons.org/licenses/by-sa/4.0/.
%

%
% \brief Firmware project chapter.
%
% \author Gabriel Mariano Marcelino <gabriel.mm8@gmail.com>
%
% \version 1.0.0
%
% \date 2021/05/12
%

\chapter{Firmware} \label{ch:firmware}

This chapter describes the main characteristics of the firmware part of the TTC module.

\section{Product tree}

The product tree of the firmware part of the TTC 2.0 module is available in \autoref{fig:product-tree-fw}. This product tree follows the architecture of the firmware, being divided according to the firmware layers.

\begin{figure}[!ht]
    \begin{center}
        
        \caption{Product tree of the firmware of the TTC 2.0 module.}
        \label{fig:product-tree-fw}
    \end{center}
\end{figure}

\section{Commands} \label{sec:commands}

To externally control and access the TTC module, some commands are available through the serial interfaces of the board. The commands are almost identical for both microcontrollers (except the command answering behavior) and are available on all interfaces. A list with the commands is available in \autoref{tab:commands}. The format of the commands answers can be seen in \autoref{tab:commands-ans}.

\begin{table}[!ht]
    \centering
    \scriptsize
    \begin{tabular}{clll}
        \toprule[1.5pt]
        \textbf{ID} & \textbf{Name} & \textbf{Content} & \textbf{Interface}\\
        \midrule
        0   & NOP               & None                                           & SPI \\
        1   & Read parameter     & Command ID (1B) + Parameter ID (1B)   & SPI \\
        2   & Write parameter   & Command ID (1B) + Parameter ID (1B) + Value (4B) & SPI \\
        3   & Transmit packet   & Command ID (1B) + Packet length (1B)  + Packet (1-220B)         & SPI/UART \\
        4   & Receive packet    & Command ID (1B)      & SPI \\
        \bottomrule[1.5pt]
    \end{tabular}
    \caption{List of command's requests.}
    \label{tab:commands}
\end{table}

\begin{table}[!ht]
    \centering
    \scriptsize
    \begin{tabular}{cll}
        \toprule[1.5pt]
        \textbf{ID} & \textbf{Name} & \textbf{Content}\\
        \midrule
        1   & Read parameter    & Command ID (1B) + Parameter ID (1B) + Value (4B) \\
        2   & Write parameter   & None \\
        3   & Transmit packet   & None \\
        4   & Receive packet    & Command ID (1B) + Packet(1-220B) \\
        \bottomrule[1.5pt]
    \end{tabular}
    \caption{Format of the command's answers.}
    \label{tab:commands-ans}
\end{table}

A description of each command is available below and the details about the protocol communication are available at \autoref{sec:server_param}.

\begin{itemize}
    \item Read parameter/variable (ID = 1): This command is used to read a parameter or variable of the TTC module (see \autoref{tab:ttc2-variables}).
    \item Write parameter/variable (ID = 2): This command is used to write a value to a given parameter or variable when allowed (see \autoref{tab:ttc2-variables}).
    \item Transmit packet (ID = 3): This command is used to transmit a packet through the radio link of each microcontroller.
    \item Receive packet (ID = 4): This command is used to read a received packet through the radio link (stored in the internal FIFO of the microcontrollers of the TTC).
\end{itemize}

\section{Variables and Parameters}\label{sec:variables}

A list of all the variables of TTC with their identification number (ID) and variable type that can be read from the sensors and peripherals can be seen in \autoref{tab:ttc2-variables}.

\begin{longtable}[c]{cL{0.72\textwidth}lc}
    \toprule[1.5pt]
    \textbf{ID} & \textbf{Name/Description} & \textbf{Type} & \textbf{Access} \\
    \midrule
    0   & Device ID (0xCC2A or 0xCC2B)                                      & uint16 & R \\
    1   & Hardware version                                                  & uint8  & R \\
    2   & Firmware version (ex.: ``v1.2.3'' = 0x00010203)                  & uint32 & R \\
    3   & Time counter in milliseconds                                       & uint32 & R \\
    4   & Reset counter                                                     & uint16 & R \\
    \multirow{18}{*}{5} & Last reset cause: & \multirow{18}{*}{uint8} & \multirow{18}{*}{R} \\
        & - 0x00 = No interrupt pending                                     &        &  \\
        & - 0x02 = Brownout (BOR)                                           &        &  \\
        & - 0x04 = RST/NMI (BOR)                                            &        &  \\
        & - 0x06 = PMMSWBOR (BOR)                                           &        &  \\
        & - 0x08 = Wakeup from LPMx.5 (BOR)                                 &        &  \\
        & - 0x0A = Security violation (BOR)                                 &        &  \\
        & - 0x0C = SVSL (POR)                                               &        &  \\
        & - 0x0E = SVSH (POR)                                               &        &  \\
        & - 0x10 = SVML\_OVP (POR)                                          &        &  \\
        & - 0x12 = SVMH\_OVP (POR)                                          &        &  \\
        & - 0x14 = PMMSWPOR (POR)                                           &        &  \\
        & - 0x16 = WDT time out (PUC)                                       &        &  \\
        & - 0x18 = WDT password violation (PUC)                             &        &  \\
        & - 0x1A = Flash password violation (PUC)                           &        &  \\
        & - 0x1C = Reserved                                                 &        &  \\
        & - 0x1E = PERF peripheral/configuration area fetch (PUC)           &        &  \\
        & - 0x20 = PMM password violation (PUC)                             &        &  \\
        & - 0x22 to 0x3E = Reserved                                         &        &  \\
    6   & Input voltage of the $\mu$C in mV                                 & uint16 & R \\
    7   & Input current of the $\mu$C in mA                                 & uint16 & R \\
    8   & Temperature of the $\mu$C in K                                    & uint16 & R \\
    9   & Input voltage of the radio in mV                                  & uint16 & R \\
    10  & Input current of the radio in mA                                  & uint16 & R \\
    11  & Temperature of the radio in K                                     & uint16 & R \\
    12  & Last valid command (uplink packet ID)                             & uint8  & R \\
    13  & RSSI of the last valid telecommand                                & uint16 & R \\
    14  & Temperature of the antenna module in K                            & uint16 & R \\
    \multirow{17}{*}{15} & Antenna module status bits:                      & \multirow{17}{*}{uint16} & \multirow{17}{*}{R} \\
        & - Bit 15: The antenna 1 is deployed (0) or not (1)                &        &   \\
        & - Bit 14: Cause of the latest activation stop for antenna 1       &        &   \\
        & - Bit 13: The antenna 1 deployment is active (1) or not (0)       &        &   \\
        & - Bit 11: The antenna 2 is deployed (0) or not (1)                &        &   \\
        & - Bit 10: Cause of the latest activation stop for antenna 2       &        &   \\
        & - Bit 9: The antenna 2 deployment is active (1) or not (0)        &        &   \\
        & - Bit 8: The antenna is ignoring the deployment switches (1) or not (0) &  &   \\
        & - Bit 7: The antenna 3 is deployed (0) or not (1)                 &        &   \\
        & - Bit 6: Cause of the latest activation stop for antenna 3        &        &   \\
        & - Bit 5: The antenna 3 deployment is active (1) or not (0)        &        &   \\
        & - Bit 4: The antenna system independent burn is active (1) or not (0) &    &   \\
        & - Bit 3: The antenna 4 is deployed (0) or not (1)                 &        &   \\
        & - Bit 2: Cause of the latest activation stop for antenna 4        &        &   \\
        & - Bit 1: The antenna 4 deployment is active (1) or not (0)        &        &   \\
        & - Bit 0: The antenna system is armed (1) or not (0)               &        &   \\
    16  & Antenna deployment status (0=never executed, 1=executed)          & uint8  & R \\
    17  & Antenna deployment hibernation (0=never executed, 1=executed)     & uint8  & R \\
    18  & TX enable (0=off, 1=on)                                           & uint8  & R/W \\
    19  & TX packet counter                                                 & uint32 & R \\
    20  & RX packet counter (valid packets)                                 & uint32 & R \\
    21  & TX packets available in the FIFO buffer                           & uint8  & R \\
    22  & RX packets available in the FIFO buffer                           & uint8  & R \\
    23  & Number of bytes of the first available packet in the RX buffer    & uint16 & R \\
    24  & Reset TTC 2.0 Module (1=starts reset sequence)                    & uint8  & W \\
    \bottomrule[1.5pt]
    \caption{Variables and parameters of the TTC 2.0.}
    \label{tab:ttc2-variables}
\end{longtable}

Each variable can be read or written using the commands ``Read Parameter'' and/or ``Write Parameter''. Some variables can just be read, as seen in the most right column of \autoref{tab:ttc2-variables}. When a variable is less than 32 bits long, it is left filled with zeros during a read or write operation (ex.: the value 0xAB becomes 0x000000AB).

\section{Layers}

The firmware flow of development goes from the low-level implementation (far right), with HAL being register-level operation, to Tasks Layer with very abstract and high-level code.

\subsection{Hardware Abstraction Layer}

The HAL layer is the API DriverLib developed by Texas Instruments; it includes register manipulating functions to accelerate development. The TTC 2.0 uses HAL to handle GPIO operations and serial communications such as SPI, UART, and I$^2$C.

\subsection{Drivers}

Driver Layer is created to have the flexibility of the HAL layer but contains only the necessary abstraction to be still generic enough to support all the functionalities needed in Devices or other Drivers modules.

\subsection{Devices}

In this level of abstraction, the devices are used to create specific configurations with the Drivers Layer to build functions used in the Tasks layer. In opposition to the Drivers layer, the Devices do not communicate between themselves and are only used inside Tasks.

\subsection{RTOS}

The TTC 2.0 uses FreeRTOS kernel. Using an RTOS-based kernel enables the system to regularly maintain routine functions such as housekeeping, sensor reading, checking for receptions, and dealing with specific delays used in hardware, such as the radio. The priority level of a task dictates who has the most preference for execution. Initial delay and period are used to determine the delay time to execute the task initialization after a boot; this regulates the time between the task executions. The stack is the amount of memory delimited to execute a task.

\subsection{System}

The System layer is used for housekeeping and management routines; it contains the system log, clock setup, and hooks. Its executions occur in almost all the TTC 2.0 abstraction layers (except the Tests layer), mostly for log purposes, as seen in Figure \ref{fig:log_info}.

\begin{figure}[!ht]
	\begin{center}
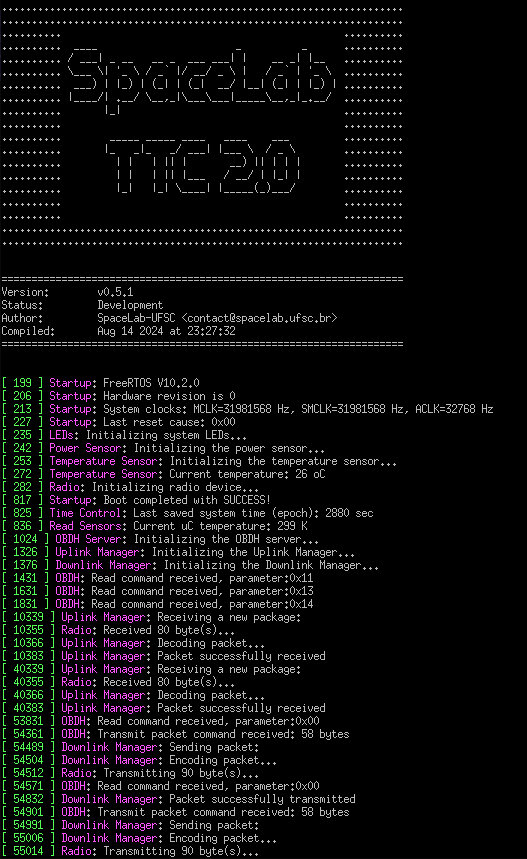
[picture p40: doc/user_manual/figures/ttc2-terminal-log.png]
		
		\caption{Example of log feedback received from TTC 2.0}
		\label{fig:log_info}
	\end{center}
\end{figure}

\subsection{Tasks}

Tasks are the FreeRTOS threads equivalent and are the uppermost abstraction layer of code inside the TTC 2.0 flow of execution. Each task is designated a priority level, initial delay, period, and stack size as shown in \autoref{tab:firmware-tasks}.

\begin{table}[!ht]
    \centering

    \begin{tabular}{lccccc}
        \toprule[1.5pt]
        \textbf{Name}          & \textbf{Priority\footnote{The priority follows a quantitative pattern, the higher the most important}} & \textbf{Initial delay [ms]} & \textbf{Period [ms]} & \textbf{Stack [bytes]} \\
        \midrule
        Antenna Deployment     & 6  & 3600000 & 100       & 150  \\
        Downlink Manager       & 3  & 550     & 150       & 2000 \\
        EPS Server             & 3  & 10000   & 750       & 1000 \\
        Heartbeat              & 1  & 2000    & 500       & 160  \\
        OBDH Server            & 5  & 200     & 100       & 2000 \\
        Radio Reset            & 5  & 60000   & 60000     & 128  \\
        Read Antenna           & 2  & 2000    & 60000     & 150  \\
        Read Sensors           & 3  & 2000    & 60000     & 128  \\
        Startup                & 6  & 0       & Aperiodic & 500  \\
        System Reset           & 2  & 0       & 36000000  & 128  \\
        Time Control           & 3  & 1000    & 1000      & 128  \\
        Uplink Manager         & 3  & 500     & 300       & 2000 \\
        Watchdog Reset         & 1  & 0       & 100       & 150  \\
        \bottomrule[1.5pt]
    \end{tabular}
    \caption{List of TTC 2.0 tasks with configuration parameters.}
    \label{tab:firmware-tasks}
\end{table}

Each of the tasks presented in \autoref{tab:firmware-tasks} is described below:

\begin{itemize}
    \item \textbf{Antenna Deployment}: Initialize the antenna sequence of deploy after 
    \item \textbf{Downlink Manager}: Monitors for radio request from other tasks and manages downlink FIFO.
    \item \textbf{EPS Server}: Read only transmit requests from UART bus.
    \item \textbf{Heartbeat}: Blinks a status LED at a rate of 1 Hz. Both microcontrollers have a status LED. This LED indicates that the scheduler is up and running.
    \item \textbf{OBDH Server}: Read requests and send response from the SPI bus.
    \item \textbf{Radio Reset}: Resets the radio at 600 seconds.
    \item \textbf{Read Antenna}: Reads antenna current status and temperature.
    \item \textbf{Read Sensors}: Reads the uC and radio temperature and power consumption. 
    \item \textbf{Startup}: Initializes all the devices and peripherals, and variables of the TTC 2.0 module (boot sequence).
    \item \textbf{System Reset}: Resets the microcontroller by software every 10 hours.
    \item \textbf{Time Control}: Manages the system time by loading the saving the time counter from/to the internal flash memory.
    \item \textbf{Uplink Manager}: Monitors the radio module for upcoming packages and stores it in memory.
    \item \textbf{Watchdog Reset}: Resets both watchdog timers (internal and external) at every 100 milliseconds.
\end{itemize}

\subsection{Libraries}

The Libraries are used for algorithm purposes and are not related to any hardware. Their function removes the redundancy of creating multiple identical structures for different driver modules.

\subsection{Tests}

Tests are used to verify and validate the Drivers and Devices' developed functionality. There are three types of tests: the static test uses the MISRA-C: 2012 \cite{misrac2012} guidelines to check for C safety standards, the unitary tests use the Cmocka\footnote{\href{https://cmocka.org/}{https://cmocka.org/}} library with mockups of the hardware, to validate the module in an algorithmic level, and the last test verifies the integration between hardware and firmware.

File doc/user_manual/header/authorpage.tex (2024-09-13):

%
% authorpage.tex
%
% Copyright The TTC 2.0 Contributors.
%
% TTC 2.0 Documentation
%
% This work is licensed under the Creative Commons Attribution-ShareAlike 4.0
% International License. To view a copy of this license,
% visit http://creativecommons.org/licenses/by-sa/4.0/.
%

%
% \brief Author page.
%
% \author Gabriel Mariano Marcelino <gabriel.mm8@gmail.com>
%
% \version 1.0.0
%
% \date 2021/04/01
%

\thispagestyle{empty}

\begin{center}

\textbf{\thetitle}

\textit{September, 2024}

\vspace{1cm}

\textbf{Project Chief:}

Eduardo Augusto Bezerra <\href{mailto:eduardo.bezerra@spacelab.ufsc.br}{eduardo.bezerra@spacelab.ufsc.br}>

\vspace{1cm}

\textbf{Authors:}

Gabriel Mariano Marcelino <\href{mailto:gabriel.marcelino@spacelab.ufsc.br}{gabriel.marcelino@spacelab.ufsc.br}> \\
André Martins Pio de Mattos <\href{mailto:andre.mattos@spacelab.ufsc.br}{andre.mattos@spacelab.ufsc.br}> \\
Miguel Boing <\href{mailto:miguel.boing@spacelab.ufsc.br}{miguel.boing@spacelab.ufsc.br}> \\

\vspace{1cm}

\textbf{Contributing Authors:}

Carlos Augusto Porto Freitas \\
Sara Vega Martinez \\
Vitória Beatriz Bianchin \\
Yan Castro de Azeredo \\

\vspace{1cm}

\textbf{Revision Control:}

\end{center}

\begin{table}[!ht]
    \begin{center}
        \begin{tabular}{cL{5cm}L{5.5cm}C{2cm}}
            \toprule[1.5pt]
            \textbf{Version} & \textbf{Author}  & \textbf{Changes}    & \textbf{Date} \\
            \midrule
            v0.0 & G. M. Marcelino           & Document creation   & 2021/04/01 \\
            v0.1 & G. M. Marcelino           & First release       & 2021/06/16 \\
            v0.2 & G. M. Marcelino           & General improvements and updates & 2022/05/17 \\
            v0.3 & G. M. Marcelino, M. Boing & General improvements and updates & 2022/11/04 \\
            v0.4 & M. Boing                  & Firmware updates & 2023/03/19 \\
            v0.5 & M. Boing                  & Firmware updates & 2023/11/01 \\
            v0.6 & M. Boing                  & Firmware updates & 2024/03/14 \\
            v1.0 & G. M. Marcelino, M. Boing & Stable release   & 2024/09/05 \\
            \bottomrule[1.5pt]
        \end{tabular}
    \end{center}
\end{table}

\vfill

\begin{figure}[!h]
	\begin{center}
		
	\end{center}
\end{figure}

\textcopyright\  2024 by SpaceLab. \thetitle. This work is licensed under the Creative Commons Attribution-ShareAlike 4.0 International License. To view a copy of this license, visit \href{http://creativecommons.org/licenses/by-sa/4.0/}{http://creativecommons.org/licenses/by-sa/4.0/}.

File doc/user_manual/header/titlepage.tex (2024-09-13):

%
% titlepage.tex
%
% Copyright The TTC 2.0 Contributors.
%
% TTC 2.0 Documentation
%
% This work is licensed under the Creative Commons Attribution-ShareAlike 4.0
% International License. To view a copy of this license,
% visit http://creativecommons.org/licenses/by-sa/4.0/.
%

%
% \brief Title page.
%
% \author Gabriel Mariano Marcelino <gabriel.mm8@gmail.com>
%
% \version 1.0.0
%
% \date 2021/04/01
%

\begin{titlepage}

\thispagestyle{empty}

\begin{flushleft}
SLB-TTC2-DOC-v1.0
\end{flushleft}

\vspace{1cm}

\begin{figure}[!ht]
    \begin{flushleft}
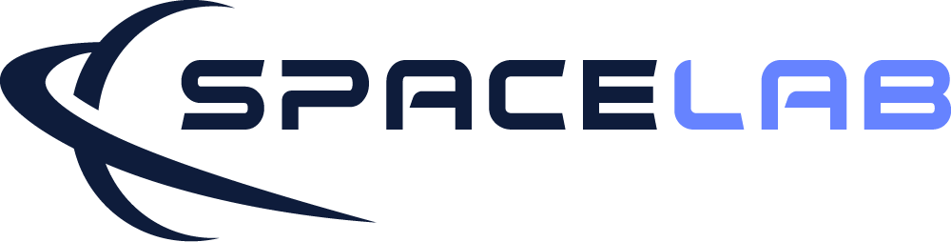
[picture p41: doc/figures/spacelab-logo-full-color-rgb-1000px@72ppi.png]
        
    \end{flushleft}
\end{figure}

\begin{flushleft}
\Huge{\textbf{\thetitle}}
\rule[0pt]{\textwidth}{5pt}
\end{flushleft}

\vspace{0.2cm}

\begin{flushleft}
\textit{\thetitle} \\
\textit{SpaceLab, Universidade Federal de Santa Catarina, Florianópolis - Brazil}
\end{flushleft}

\vfill
\vfill

\begin{flushright}
September 2024
\end{flushright}

\end{titlepage}

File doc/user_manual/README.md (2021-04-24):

# TTC 2.0 Documentation

Documentation of the Telemetry, Tracking and Command 2.0.

## Dependencies

* ```latexmk```

## Generating the PDF file

```
make
```

## License

This document is licensed under Creative Commons Attribution-ShareAlike 4.0 International.

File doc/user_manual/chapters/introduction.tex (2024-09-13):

%
% introduction.tex
%
% Copyright The TTC 2.0 Contributors.
%
% TTC 2.0 Documentation
%
% This work is licensed under the Creative Commons Attribution-ShareAlike 4.0
% International License. To view a copy of this license,
% visit http://creativecommons.org/licenses/by-sa/4.0/.
%

%
% \brief Introduction chapter.
%
% \author Gabriel Mariano Marcelino <gabriel.mm8@gmail.com>
%
% \version 1.0.0
%
% \date 2021/04/01
%

\chapter{Introduction} \label{ch:introduction}

The TTC 2.0 is a Telemetry, Tracking and Command module designed for nanosatellites. It is one of the service modules developed for the GOLDS-UFSC CubeSat Mission \cite{floripasat2}, and part of the FloripaSat-2 platform \cite{marcelino2023}.

The module is a direct upgrade from the TTC of FloripaSat-1 \cite{ttc-fsat}, which grants a flight heritage rating. The improvements focus on providing a cleaner and more generic implementation than the previous version, more reliability in software and hardware implementations, and adaptations for the new mission requirements. All the project, source, and documentation files are available freely on a GitHub repository \cite{ttc2-repo} under the GPLv3 (firmware) and CERN OHLv2 (hardware) licenses.

\begin{figure}[!h]
	\begin{center}
		
		\caption{3D view of the TTC 2.0 PCB.}
		\label{fig:pcb-3d}
	\end{center}
\end{figure}

\section{Product tree}

The product tree of the TTC 2.0 module can be divided into three branches: hardware, firmware, and documentation. A diagram of the product tree is available in \autoref{fig:product-tree}.

\begin{figure}[!ht]
    \begin{center}
        
        \caption{Product tree of the TTC 2.0 module.}
        \label{fig:product-tree}
    \end{center}
\end{figure}

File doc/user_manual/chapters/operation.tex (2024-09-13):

%
% operation.tex
%
% Copyright The TTC 2.0 Contributors.
%
% TTC 2.0 Documentation
%
% This work is licensed under the Creative Commons Attribution-ShareAlike 4.0
% International License. To view a copy of this license,
% visit http://creativecommons.org/licenses/by-sa/4.0/.
%

%
% \brief Introduction chapter.
%
% \author Gabriel Mariano Marcelino <gabriel.mm8@gmail.com>
%
% \version 1.0.0
%
% \date 2022/10/09
%

\chapter{Operation} \label{ch:operation}

This chapter describes general aspects of the TTC operation, like details of the used communication protocol, how to transmit a packet, how the telecommand reception works, and so on.

\section{Packet transmission}

    To transmit a packet, the command ``Transmit Packet'' must be used (\autoref{sec:commands}). When the TTC receives this command through one of its command interfaces, a new NGHam packet is generated with the command content as the packet's payload. After the NGHam packet is generated, it is transmitted immediately through the air using the respective TTC's radio.

\section{Telecommand reception}

When a new valid telecommand is received, it is stored in an internal queue with five positions and 300 bytes available for each position. The new packet is discarded if the queue is full and there are no available positions to store the telecommands.

A telecommand is only stored if it is a valid NGHam packet, and only the payload of the NGHam packet is stored. Each telecommand can be up to 220 bytes long, according to the NGHam protocol definitions.

The received and stored telecommand can be read with the command read packet, as described in \autoref{sec:commands}. After a telecommand is read, it is deleted from the internal queue of the TTC module. The number of available telecommands and the length in bytes of the first queue position can be read using the command ``Read Parameter'', as also described in Sections \ref{sec:commands} and \ref{sec:variables}.

\section{Communication protocol}

The communication protocol used with the satellite is the NGHam \cite{pyngham-doc}. The NGHam protocol stands for Next Generation Ham Radio, a protocol designed for packet communication. It is similar to the classical AX.25 \cite{ax25} protocol, but with the idea of using a FEC (Forward Error Correction) algorithm to increase the robustness, as defined in \cite{lofaldli2016}:

\begin{quote}
``...a link protocol partly inspired by AX.25. To improve the link reliability, it features Reed Solomon codes for Forward Error Correction (FEC). This makes the data transmission more robust compared to, i.e., AX.25, which does not directly implement FEC on the link layer.''
\end{quote}

It was initially developed in the context of the CubeSat NUTS-1 (NTNU Test Satellite) development by the Norwegian University of Science and Technology (NTNU). This library is based on the implementation of Jon Petter Skagmo (LA3JPA), available in \cite{ngham}.

\subsection{Packet fields}

The \autoref{fig:ngham-pkt} presents a diagram with packet format and the data fields of the NGHam protocol.

\begin{figure}[!ht]
    \begin{center}
        
        \caption{Format of an NGHam packet.}
        \label{fig:ngham-pkt}
    \end{center}
\end{figure}

Next, there is a brief description of each one of those fields.

\subsubsection{Preamble}

Considering a data rate of 9600 bps, 4 bytes are typically used for the preamble. This sequence is an alternation of ones and zeros: 4$\times$ 0xAA (0b10101010).

\subsubsection{Sync. word}

The sync. word is a sequence of bits used for packet synchronization. With this sequence, the receiver can detect the start of a new packet. In NGHam, the sync. word is composed of 32 bits, following the pattern: 0x5D, 0xE6, 0x2A, 0x7E.

\subsubsection{Size tag}

This field indicates one of the seven possible packet sizes. It is a 24 bits tag and is made very robust by keeping a hamming distance of 13 bits between all vectors. The seven possible tags are listed in \autoref{tab:ngham-sizes}.

\begin{table}[!ht]
    \centering
    \begin{tabular}{llll}
        \toprule[1.5pt]
        \textbf{Size Num.} & \textbf{Tag} & \textbf{Reed-Solomon Config.} & \textbf{Max. Data Size} \\
        \midrule
        1 & 59, 73, 205   & RS(47, 31)   & up to 28 bytes of data \\
        2 & 77, 218, 87   & RS(79, 63)   & up to 60 bytes of data \\
        3 & 118, 147, 154 & RS(111, 95)  & up to 92 bytes of data \\
        4 & 155, 180, 174 & RS(159, 127) & up to 124 bytes of data \\
        5 & 160, 253, 99  & RS(191, 159) & up to 156 bytes of data \\
        6 & 214, 110, 249 & RS(223, 191) & up to 188 bytes of data \\
        7 & 237, 39, 52   & RS(255, 223) & up to 220 bytes of data \\
        \bottomrule[1.5pt]
    \end{tabular}
    \caption{NGHam packets sizes.}
    \label{tab:ngham-sizes}
\end{table}

\subsubsection{Reed-Solomon block}

The Reed-Solomon code block (or just RS block) is the field with packet payload and parity data. It is divided into two parts: data and parity bytes. The data bytes are subdivided into four fields: header, payload, checksum, and padding. Each one of these fields is described below.

\paragraph{Header}

The header byte is the first data byte of the RS block. It is divided as presented in \autoref{tab:ngham-header-flags}.

\begin{table}[!ht]
    \centering
    \begin{tabular}{ll}
        \toprule[1.5pt]
        \textbf{Bits} & \textbf{Purpose} \\
        \midrule
        7 to 6  & Reserved \\
        5       & Extension on \\
        4 to 0  & Padding size (in bytes) \\
        \bottomrule[1.5pt]
    \end{tabular}
    \caption{NGHam header flags.}
    \label{tab:ngham-header-flags}
\end{table}

The extension bit indicates if the extension frame is enabled or not. The padding size bits are the number of padding bytes presented in the respective packet (0 to 31).

\paragraph{Payload}

The payload field is where the “useful” packet data is stored. As presented in the Size Tag field description above, each of the seven size groups allows a maximum number of bytes in the packet payload. The maximum possible length of the payload for an NGHam packet is 220 bytes. If more data need to be transmitted, it should be divided into chunks of 220 bytes and transmitted in separate packets.

\paragraph{Checksum}

There is a checksum field after the payload data to ensure data correctness and a first stage before running the Reed-Solomon correction algorithm. The used checksum algorithm is the CRC16-CCITT 5, with the following configuration:

\begin{itemize}
    \item \textbf{Polynomial}: 0x1021
    \item \textbf{Initial value}: 0xFFFF
    \item \textbf{Final XOR value}: 0xFFFF
\end{itemize}

The CRC16 value is computed from the header and the payload fields. If the CRC16 value is correct, the Reed-Solomon chain is skipped, and the packet is directly considered valid. This way, the checksum field also allows a performance improvement.

\paragraph{Padding}

To ensure the right packet length for the Reed-Solomon coding in use, if the payload content is less than the maximum allowed, the data field of the RS block is padded with zeros. The number of padding bytes is declared in the header byte (bits 4-0).

\paragraph{Parity data}

This field is reserved for the computed parity bytes of the Reed-Solomon coding algorithm. The used implementation of the RS algorithm is based on the famous FEC library developed by Phil Karn (KA9Q) 6. This field can be 16 or 32 bytes long, depending on the payload length, and consequently, the adopted RS scheme described in \autoref{tab:ngham-parity}.

\begin{table}[!ht]
    \centering
    \begin{tabular}{lll}
        \toprule[1.5pt]
        \textbf{Size Num.} & \textbf{Reed-Solomon Config.} & \textbf{Parity bytes} \\
        \midrule
        1 & RS(47, 31)   & 16 \\
        2 & RS(79, 63)   & 16 \\
        3 & RS(111, 95)  & 16 \\
        4 & RS(159, 127) & 32 \\
        5 & RS(191, 159) & 32 \\
        6 & RS(223, 191) & 32 \\
        7 & RS(255, 233) & 32 \\
        \bottomrule[1.5pt]
    \end{tabular}
    \caption{NGHam parity sizes.}
    \label{tab:ngham-parity}
\end{table}

For the Reed-Solomon framing, the following configuration is used:

\begin{itemize}
    \item \textbf{Symbol size}: 8
    \item \textbf{GF polynomial}: 0x187 (coefficients form)
    \item \textbf{First root of RS code generator polynomial}: 112 (index form)
    \item \textbf{Primitive element}: 11
    \item \textbf{Number of roots}: 16 or 32 (table above)
\end{itemize}

\subsection{Scrambling}

Before transmitting a packet, the RS code block is scrambled by making a byte xor operation with a pre-generated table based on the polynomial $x^{8} + x^{7} + x^{5} + x^{3} + 1$ (defined in the CCSDS 131.0-B-3 standard \cite{ccsds}).

When the receiver receives a packet, it also performs the same operation to de-scramble the RS code block and gets the original content of the RS part of the packet.

By scrambling the packets, long sequences of ones or zeros are avoided by guaranteeing a good bit transition along the whole packet. More information about packet scrambling (or randomization) can be found in \cite{ccsds} (section 8.3).

\section{Flow of execution}
The TTC module operates accordingly to the flowchart from Figure \ref{fig:ttc_flowchart}. Its routine consists of frequent checks for uplink packages or requests from OBDH or EPS to downlink data. Also, by default TTC has protective measures to reset the radio between 600 seconds and the microcontroller after 10 hours.

\begin{figure}[!ht]
    \begin{center}
        
        \caption{TTC 2.0 flowchart of execution.}
        \label{fig:ttc_flowchart}
    \end{center}
\end{figure}

\section{Server parameter}\label{sec:server_param}

There are two main serial ports accessible to communicate with the TTC module a UART that is accessible only for the radio 1 and can only transmit packages. The other port is an SPI and is possible to communicate individually with each microcontroller and you can requisite all the commands and parameters (see Tables \ref{tab:commands} and \ref{tab:ttc2-variables}). The protocol communication is described below.

\subsection{EPS server}

The EPS Server is in RX mode and only the Transmit packet command (ID=3) is available. To transmit a package the first byte shall be the command (0x03) followed by the packet. The UART configuration is resumed on Table \ref{tab:eps_config}. This serial port can be accessed via the pin 5 of the PC104-H2 pin 7 is connected to TX but is not utilized, see Table \ref{tab:pc104-pinout}.

\begin{table}[!ht]
    \centering
    \begin{tabular}{lc}
        \toprule[1.5pt]
        \textbf{Configuration Parameter} & \textbf{Value}\\
        \midrule
        Clock               & 1 MHz       \\
        Baud Rate           & 115200 bps  \\
        Data Bits           & 8           \\
        Parity              & No parity   \\
        Stop Bits           & 1           \\
        \bottomrule[1.5pt]
    \end{tabular}
    \caption{EPS Server configuration parameter.}
    \label{tab:eps_config}
\end{table}

\begin{figure}[!ht]
    \begin{center}
        
        \caption{EPS Server communication diagram description.}
        \label{fig:eps-server-communication}
    \end{center}
\end{figure}

\subsection{OBDH server}

The OBDH Server can be used for full communication and all the commands are implemented for this port. The TTC operates as half-duplex with the commands having a request and a followed by response (except for command Write parameter ID=2 that only uses a request). For commands that need a response it is required to leave a interval of at least 100ms from the request to the response. Each communication part, for both sides, in all commands starts with the preamble byte (0x7E) that can be used to detect and synchronize wrong transactions. When each side is communicating the listening side needs to send 0x00 while the other side transmits.
All the request have seven bytes length including the preamble, the response for command ID=1 also has 7 bytes as fixed size, the response from commands ID=3 and ID=4 have a variable size accordingly to the request. The communication for each case is described in Figure \ref{fig:obdh-server-communication}. The TTC operates in SPI mode 0 and was tested with 1 MHz clock.

\begin{figure}[!ht]
    \begin{center}
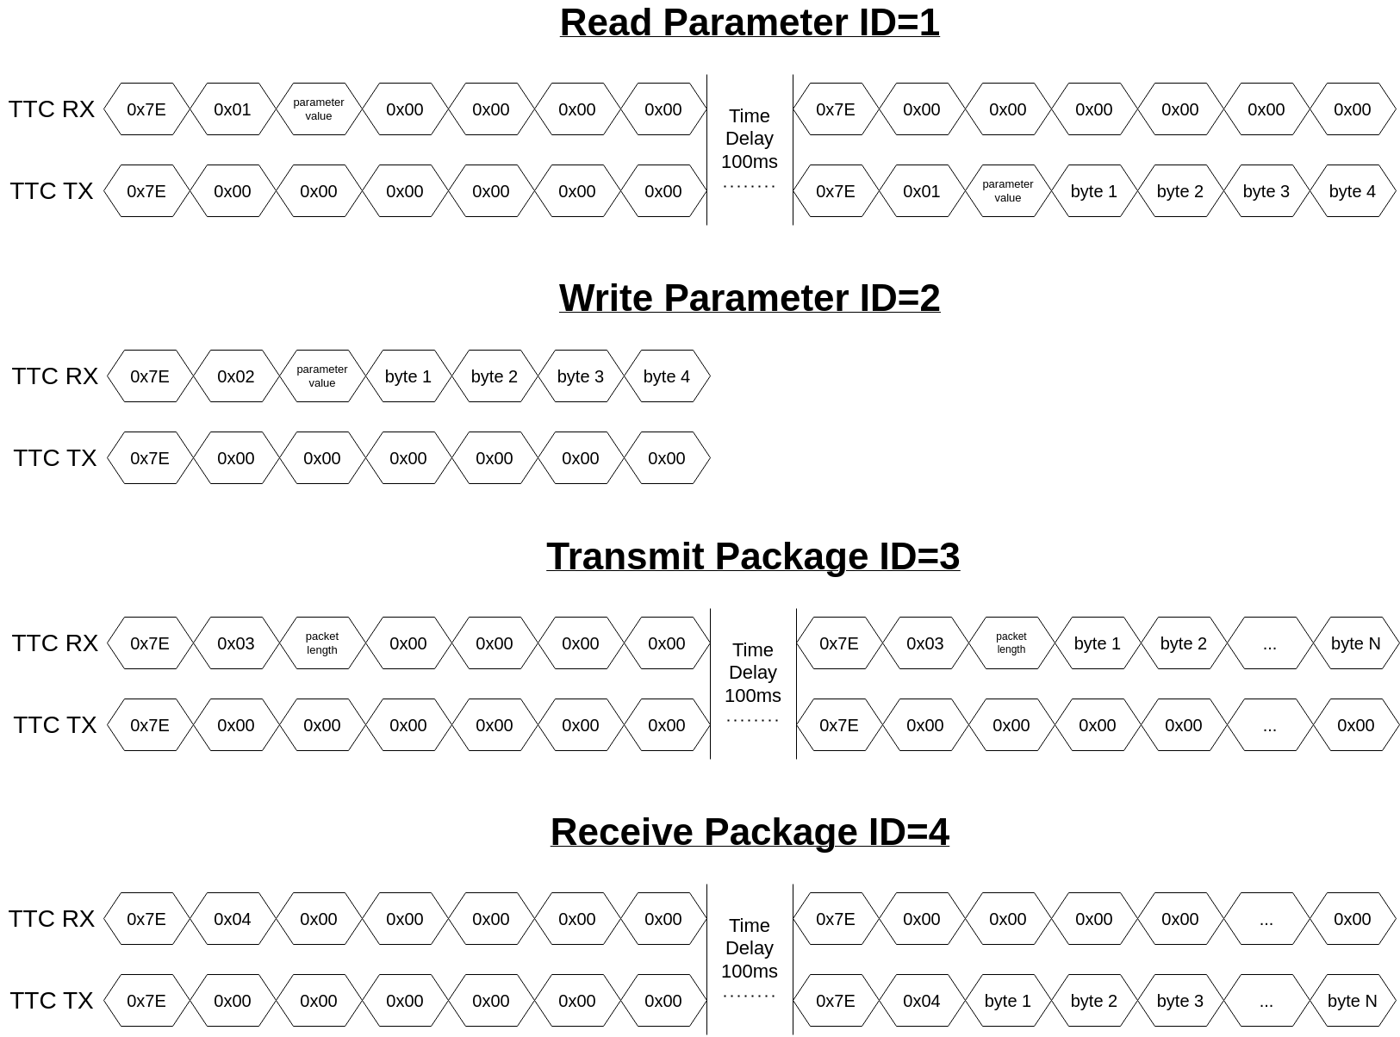
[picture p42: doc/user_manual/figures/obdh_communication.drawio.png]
        
        \caption{OBDH Server communication diagram description.}
        \label{fig:obdh-server-communication}
    \end{center}
\end{figure}

\begin{table}[!ht]
    \centering
    \begin{tabular}{lc}
        \toprule[1.5pt]
        \textbf{Configuration Parameter} & \textbf{Value}\\
        \midrule
        Mode  & 0                \\
        Clock & 200 kHz to 1 MHz \\
        \bottomrule[1.5pt]
    \end{tabular}
    \caption{OBDH Server configuration parameter.}
    \label{tab:eps_config}
\end{table}

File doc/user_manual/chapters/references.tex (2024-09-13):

%
% references.tex
%
% Copyright The TTC 2.0 Contributors.
%
% TTC 2.0 Documentation
%
% This work is licensed under the Creative Commons Attribution-ShareAlike 4.0
% International License. To view a copy of this license,
% visit http://creativecommons.org/licenses/by-sa/4.0/.
%

%
% \brief References chapter.
%
% \author Gabriel Mariano Marcelino <gabriel.mm8@gmail.com>
%
% \version 1.0.0
%
% \date 2021/04/01
%

\bibliography{references/ttc2,%
              references/ttc2-repo,%
              references/floripasat2,%
              references/ttc-fsat,%
              references/lofaldli2016,%
              references/ax25,%
              references/ngham,%
              references/ccsds,%
              references/pyngham-doc,%
              references/misrac2012,%
              references/nasa-handout,%
              references/marcelino2023,%
              references/ccs-studio,%
              references/ttc2-releases,%
              references/sl-transmitter,%
              references/sl-decoder,%
              references/references}

\addcontentsline{toc}{chapter}{References}

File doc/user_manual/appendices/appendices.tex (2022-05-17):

%
% appendices.tex
%
% Copyright The TTC 2.0 Contributors.
%
% TTC 2.0 Documentation
%
% This work is licensed under the Creative Commons Attribution-ShareAlike 4.0
% International License. To view a copy of this license,
% visit http://creativecommons.org/licenses/by-sa/4.0/.
%

%
% \brief Appendices.
%
% \author Gabriel Mariano Marcelino <gabriel.mm8@gmail.com>
%
% \version 0.2.0
%
% \date 2022/04/22
%

\begin{appendices}

\input{appendices/test_report_v011}

\end{appendices}

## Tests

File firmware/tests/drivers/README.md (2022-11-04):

# Unit tests of the drivers

* ISIS Antenna
* Si446x
* TCA4311A
* INA22x

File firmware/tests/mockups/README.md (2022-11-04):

# Mockups of the unit tests

## Drivers

* ADC
* Flash
* GPIO
* I2C
* ISIS Antenna
* Si446x
* SPI
* SPI Slave
* TPS382x
* UART
* Watchdog

## Devices

* Radio

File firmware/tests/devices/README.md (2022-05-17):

# Unit tests of the devices

* Antenna
* LEDs
* Media
* Power Sensor
* Radio
* Temperature Sensor
* Watchdog

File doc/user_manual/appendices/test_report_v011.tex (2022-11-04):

%
% test_report_v011.tex
%
% Copyright The TTC 2.0 Contributors.
%
% TTC 2.0 Documentation
%
% This work is licensed under the Creative Commons Attribution-ShareAlike 4.0
% International License. To view a copy of this license,
% visit http://creativecommons.org/licenses/by-sa/4.0/.
%

%
% \brief Test report of the v0.1.1 hardware.
%
% \author Gabriel Mariano Marcelino <gabriel.mm8@gmail.com>
%
% \version 0.2.0
%
% \date 2022/04/22
%

\chapter{Test Report of v0.1.1 Version} \label{anx:test-report-v011}

This appendix is a test report of the first manufactured and assembled PCB (version v0.1.1).

\begin{itemize}
    \item \textbf{PCB manufacturer}: PCBWay (China)
    \item \textbf{PCB assembly}: PCBWay (China)
    \item \textbf{PCB arrival date}: 2022/04/18
    \item \textbf{Execution date}: 2022/04/22 to 2022/04/29
    \item \textbf{Tester}: Gabriel M. Marcelino, Vitória B. Bianchin and Miguel Boing
    \item \textbf{DNP components}: J\_P10, J\_P4, J\_P11, J\_P5, J\_P9, J\_P12, J\_P13, J\_P14, R7, R24, V2, V4, ESD, U12, U13
\end{itemize}

\section{Visual Inspection}

\begin{itemize}
    \item \textbf{Test description/Objective}: Inspection of the board, visually and with a multimeter, searching for fabrication and assembly failures.
    \item \textbf{Material}:
        \begin{itemize}
            \item Multimeter Fluke 17B+
            \item Digital microscope (1000x)
        \end{itemize}
    \item \textbf{Results}: The results of this test can be seen in Figures \ref{fig:ttc2-v011-top} (top view of the board) and \ref{fig:ttc2-v011-bottom} (bottom view of the board).
    \item \textbf{Conclusion}: No problems were identified on this test.
\end{itemize}

\begin{figure}[!ht]
    \begin{center}
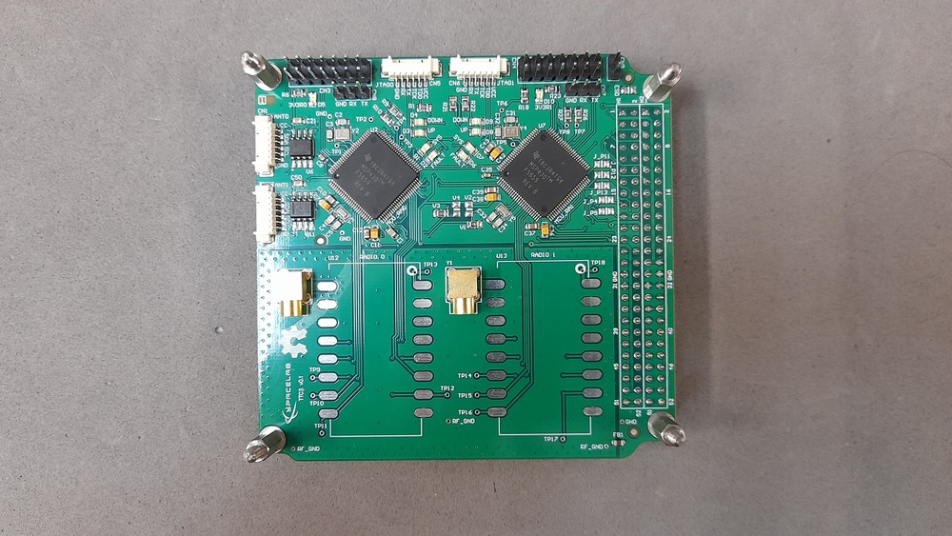
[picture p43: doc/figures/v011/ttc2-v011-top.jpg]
        
        \caption{Top view of the TTC 2.0 v0.1.1 board.}
        \label{fig:ttc2-v011-top}
    \end{center}
\end{figure}

\begin{figure}[!ht]
    \begin{center}
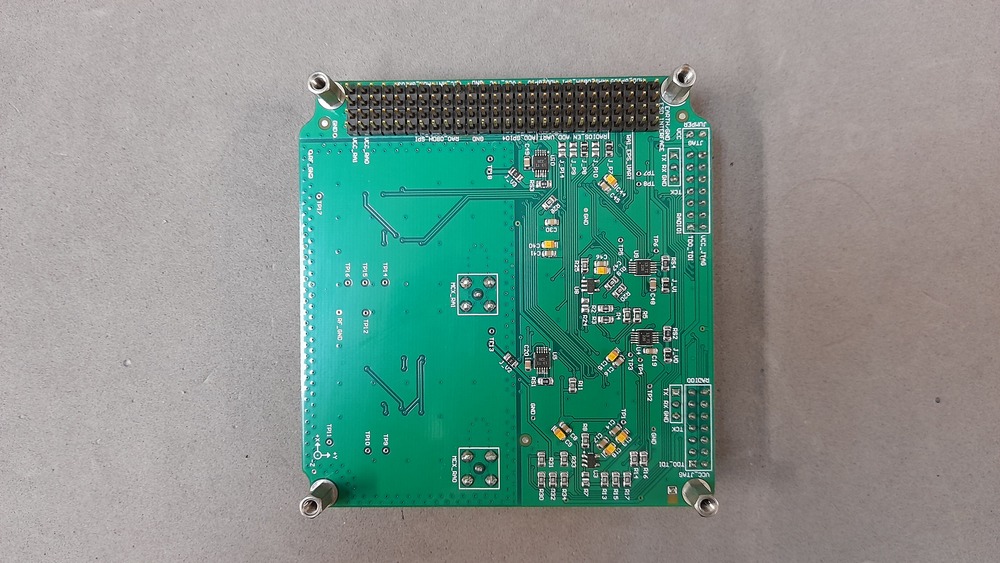
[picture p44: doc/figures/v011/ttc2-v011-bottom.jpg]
        
        \caption{Bottom view of the TTC 2.0 v0.1.1 board.}
        \label{fig:ttc2-v011-bottom}
    \end{center}
\end{figure}

\section{Firmware Programming}

\begin{itemize}
    \item \textbf{Test description/Objective}: Inspection of the board, visually and with a multimeter, searching for fabrication and assembly mistakes.
    \item \textbf{Material}:
        \begin{itemize}
            \item Code Composer Studio v11.2.0
            \item MSP-FET Flash Emulation Tool
            \item USB-UART converter
            \item Screen (Linux software)
        \end{itemize}
    \item \textbf{Results}: %The results of this are available in \autoref{fig:log-first-boot}, where the log messages of the first boot of the board can be seen.
    \item \textbf{Conclusion}: %No problems were identified on this test.
\end{itemize}

%\begin{figure}[!ht]
%    \begin{center}
%        \includegraphics[width=0.7\columnwidth]{figures/v011/log-first-boot.png}
%        \caption{Log messages during the first boot.}
%        \label{fig:log-first-boot}
%    \end{center}
%\end{figure}

\section{Communication Busses}

\begin{itemize}
    \item \textbf{Test description/Objective}: %Test the communication busses of the board, as listed below:
%        \begin{itemize}
%            \item I$^{2}$C Port 0
%            \item I$^{2}$C Port 1
%            \item I$^{2}$C Port 2
%        \end{itemize}
    \item \textbf{Material}:
        \begin{itemize}
            \item Saleae Logic Analyzer (24 MHz, 8 channels)
            \item Saleae Logic software (v1.2.18)
            \item MSP-FET Flash Emulation Tool
        \end{itemize}
    \item \textbf{Results}: %The results of this test can be seen in Figures \ref{fig:test-i2c-0}, \ref{fig:test-i2c-1} and \ref{fig:test-i2c-2}.
    \item \textbf{Conclusion}: %No problems were identified on this test, all buses are working as expected.
\end{itemize}

\section{Sensors}

\subsection{Input Voltage}

\begin{itemize}
    \item \textbf{Test description/Objective}: Verify the input voltage measurements of the board.
    \item \textbf{Material}:
        \begin{itemize}
            \item Code Composer Studio v11
            \item MSP-FET Flash Emulation Tool
            \item USB-UART converter
            \item Screen (Linux software)
        \end{itemize}
    \item \textbf{Results}: .
    \item \textbf{Conclusion:} No problems were identified on this test.
\end{itemize}

\subsection{Input Current}

\begin{itemize}
    \item \textbf{Test description/Objective}: Verify the input current measurements of the board.
    \item \textbf{Material}:
        \begin{itemize}
            \item Code Composer Studio v11
            \item MSP-FET Flash Emulation Tool
            \item USB-UART converter
            \item Screen (Linux software)
        \end{itemize}
    \item \textbf{Results}: .
    \item \textbf{Conclusion:} No problems were identified on this test.
\end{itemize}

\section{Conclusion}

No major problems were identified during the executed tests, all peripherals all working as expected.

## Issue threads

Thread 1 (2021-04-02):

Hardware: List the updates and improvements

mgm8, 2021-04-02:
- Apply the SpaceLab standard to the schematics and the layout
    - Improve labels
    - Improve the debug pins
    - Add status leds
    - Add version resistors
    - Fix footprints and components
- Add the TX pin to the EPS communication bus
- Change the RF connectors by the through-hole version
- Add a second microcontroller to control the downlink/uplink radio module
- Change the MSP430 microcontroller by a version with FRAM memory
- Add buffer to the communication buses
- Add more optional signals to the PC-104 bus
- Add voltage/current sensors (uC and radio modules)
- Add a CAN bus
- Isolate the SPI bus of the radio modules

andrempmattos, 2021-04-24:
**Done:**
- Apply the SpaceLab standard to the schematics and the layout
    - Improve labels
    - Improve the debug pins
    - Add status leds
    - Add version resistors
    - Fix footprints and components
- Add the TX pin to the EPS communication bus
- Change the RF connectors by the through-hole version
- Add a second microcontroller to control the downlink/uplink radio module
- Add buffer to the communication buses **(only for the antenna interface)**
- Add more optional signals to the PC-104 bus
- Add voltage/current sensors (uC and radio modules)

**Not planned for this version:**
- Change the MSP430 microcontroller by a version with FRAM memory
- Add a CAN bus
- Isolate the SPI bus of the radio modules

Closed 2021-04-24.

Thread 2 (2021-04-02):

Hardware: Apply the SpaceLab standard to the schematics and the layout

andrempmattos, 2021-04-02:
Improve nomenclature and folder structure
Improve labels
Improve the debug pins
Improve the mechanical holes
Improve the layers organization
Improve the outputs and documentation
Add status leds
Fix footprints and components

Closed 2021-04-24.

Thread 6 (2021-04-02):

Hardware: Add voltage/current sensors

mgm8, 2021-04-02:
Add current and voltage sensors to the power bus of the microcontrollers, and also, if possible, to the radio modules power sources.

andrempmattos, 2021-04-13:
Check if a pull-up for alert pin is required

Closed 2021-04-24.

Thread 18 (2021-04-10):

Hardware: Replace component ID links from old libraries

YanAzer, 2021-04-10:
Some componentes are directly linked to old EPS and Floripasat libraries, full replacement may be needed to update the components symbol and footprint characteristics.

Closed 2021-04-24.

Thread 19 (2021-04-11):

Firmware: Develop a driver of the INA226 sensor

mgm8, 2021-04-11:
[https://www.ti.com/product/INA226](https://www.ti.com/product/INA226)

mgm8, 2022-03-09:
We already have an initial structure of the driver: [https://github.com/spacelab-ufsc/ttc2/tree/dev_firmware/firmware/drivers/ina22x](https://github.com/spacelab-ufsc/ttc2/tree/dev_firmware/firmware/drivers/ina22x)

yurigazzoni, 2022-03-12:
I will need the values of Rshunt and of the maximum expected current to calibrate the register, to correctly measure the current, @mgm8.

mgm8, 2022-03-12:
> I will need the values of Rshunt and of the maximum expected current to calibrate the register, to correctly measure the current, @mgm8.

The Rshunt value is available in the schematics (sheets 3 and 4): [board_full_pdf.pdf](https://github.com/spacelab-ufsc/ttc2/blob/dev_hardware/hardware/outputs/board_schematics/board_full_pdf.pdf)

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

**Obs**.: All sensors use the same value for the shunt resistor (0,1 Ohm).

For the maximum expected current, we can consider 1000 mA for the radios, and 100 mA for the MCUs (but maybe we will have to calibrate these values when testing the firmware in a PCB).

**Tip**: Put these variables as parameters of the [configuration structure](https://github.com/spacelab-ufsc/ttc2/blob/72f6e7801ca760e01a35dbdb058a0b54ce0dcb9b/firmware/drivers/ina22x/ina22x.h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) of the driver. This way it will be easier to change the values in the higher layers of the firmware or reuse the driver.

miguelboing, 2022-06-28:
INA22x Battery Test:
* Use calibration values for uC only:
    config.cal= 10240;
    config.lsb_current = 5e-6;

- [ ] 1. Initialize the ina22x sensor (ina22x_init);
- [ ] 2. Configure with (ina22x_configuration):
    - [ ] avg_mode = 1 sample; bus_voltage_conv_time = 140u; shunt_voltage_conv_time = 140u; op_mode = Shunt and Bus, Triggered;
    Check if config_mask is correct;
    - [ ] avg_mode = 128 samples; bus_voltage_conv_time = 588u; shunt_voltage_conv_time = 588u; op_mode =Shunt Voltage,
    Check if config_mask is correct;
- [ ] 3.  Calibrate ina22x sensor for uC (ina22x_calibration);
- [ ] 4. Read Configuration Register (ina22x_read_reg);
- [ ] 5. Read Calibration Register (ina22x_read_reg);
- [ ] 6. Read manufacturer ID (ina22x_get_manufacturer_id);
- [ ] 7. Read DIE ID (ina22x_get_die_id);
- [ ] 8. Read all measurement registers (ina22x_read_reg);
- [ ] 9. Read all raw measurement with functions and compare with item 8;
- [ ] 10. Read converted measurements and compare with item 9;

miguelboing, 2022-07-20:
[Tutorial](https://training.ti.com/programming-power-settings) used to program the calibration register.

Closed 2022-11-04.

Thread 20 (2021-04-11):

Firmware: Develop a "power sensor" device

mgm8, 2021-04-11:

miguelboing, 2022-08-23:
Power Sensor Battery Test:

- [ ] Initialize power sensor (power_sensor_init());
- [ ] Check read individual function (try both scales, try both devices);
- [ ] Check read function (both devices);

miguelboing, 2022-08-23:
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

Closed 2022-11-04.

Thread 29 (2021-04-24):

Hardware: Improve silkscreen labels

andrempmattos, 2021-04-24:
There are a lot of improvements for the labels:
- Placement
- Pinout
- Connectors purpose (e.g., ant interface)
- Testpoints
- GND quick access
- LEDs function

Closed 2021-05-02.

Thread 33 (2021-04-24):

Hardware: Review schematics and report problems

andrempmattos, 2021-04-24:

mgm8, 2021-04-25:
* The section "OBDH BYPASS CONTROL OVER RADIO 0" can be removed #34.
* Add an interrupt pin ("SPI INT") to the SPI interfaces of the PC-104 bus #35.

andrempmattos, 2021-05-02:
@YanAzer suggestions also added

Closed 2021-05-02.

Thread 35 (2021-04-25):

Hardware: Add an interrupt pin to the SPI interfaces of the PC-104

mgm8, 2021-04-25:
With an interrupt GPIO, the slaves can signalize the master when data is ready to read.

andrempmattos, 2021-05-02:
For each MCU, an interrupt pin was added from pin 57 (interrupt capable) to the PC-104 (H1-7 and H1-9).

RA0_SPI_OBDH_INT: (MCU0 P4.7) --> PC-104 (H1-9) [available in OBDH with interrupt capability, P1.1]
RA1_SPI_OBDH_INT: (MCU1 P4.7) --> PC-104 (H1-7) [available in OBDH with interrupt capability, P1.3]

Closed 2021-05-02.

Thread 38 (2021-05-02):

Hardware: Review BOM and print the full schematic again (to include BOM in pdf)

andrempmattos, 2021-05-02:

YanAzer, 2021-05-12:
U4, U5, U9 and U10 missing partnumber parameter with the right format, the "Manufacturer_Part_Number" format is not acquired automatically by the BOM generation.

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

YanAzer, 2021-05-12:
- [CRCW08050000Z0EA](https://www.digikey.com/en/products/detail/vishay-dale/CRCW08050000Z0EA/1175125) with wrong description, change 1/16W to 1/8W.
- [RC0805FR-0747KL](https://www.digikey.com/en/products/detail/yageo/RC0805FR-0747KL/727973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) with wrong description, change 1/16W to 1/8W.
-[SR732ATTER100F](https://br.mouser.com/ProductDetail/KOA-Speer/SR732ATTER100F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) with wrong description, change 1/8W to 1/3W.
-[53398-0671](53398-0671) with wrong partnumber should be 53261-0671 (right angle version)
- [AC0805FR-13100KL](https://www.digikey.com/en/products/detail/yageo/AC0805FR-13100KL/13694083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) with wrong footprint, change to 0603
-[BLM21PG300SN1D](https://www.digikey.com/en/products/detail/murata-electronics/BLM21PG300SN1D/584262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) with wrong description, change to 4A
- [SSW-126-04-G-D](https://www.samtec.com/products/ssw-126-04-g-d) don't forget to add quantity to 2

Closed 2021-06-04.

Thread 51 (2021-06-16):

Hardware: Fix fabrication information on sheet layer for flight model

YanAzer, 2021-06-16:
Details such as: surface treatment, pcb color and specified no silkcreen need to be updated. Adding IPC class 3 specification may be useful.

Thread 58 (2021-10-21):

Firmware: Add a slave mode to the SPI driver

mgm8, 2021-10-21:

miguelboing, 2022-05-23:
The SPI interruption vectors are in conflict with the ones from UART. Probably we need to create one vector for each USCI with both SPI and UART interruptions.

mgm8, 2022-05-25:
> The SPI interruption vectors are in conflict with the ones from UART. Probably we need to create one vector for each USCI with both SPI and UART interruptions.

As discussed, we will create a separated driver to handle all the ISR routines, as described in #85 .

Closed 2022-05-31.

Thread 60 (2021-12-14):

Firmware: Develop a driver for the SX127x transceiver

mgm8, 2021-12-14:
Reference: [https://www.semtech.com/products/wireless-rf/lora-core/sx1278](https://www.semtech.com/products/wireless-rf/lora-core/sx1278)

miguelboing, 2023-01-05:
- [ ]

miguelboing, 2023-01-05:
Implementation progress:

- [ ] sx127x_init(void);
- [ ] sx127x_rx_init(void);
- [ ] sx127x_tx_packet(uint8_t *data, uint16_t len);
- [ ] sx127x_rx_packet(uint8_t *data, uint16_t *len);
- [ ] sx127x_wait_irq(uint8_t irq_mask);
- [ ] sx127x_enter_standby_mode(void);
- [ ] sx127x_enter_sleep_mode(void);
- [ ] sx127x_clear_interrupt(void);
- [ ] sx127x_set_frequency(uint32_t freq);
- [ ] sx127x_set_rf_param(uint8_t bw, uint8_t cr, uint8_t sf, uint8_t crc);
- [ ] sx127x_set_preamble_len(uint16_t len);
- [ ] sx127x_set_header_mode(uint8_t mode);
- [ ] sx127x_set_payload_len(uint8_t len);
- [ ] sx127x_set_tx_power(uint8_t pwr);
- [ ] sx127x_set_rx_timeout(uint16_t symb_timeout);
- [ ] sx127x_read_rssi(uint8_t mode, uint8_t rssi_val);
- [ ] sx127x_power_on_reset(void);
- [ ] sx127x_config(void);
- [ ] sx127x_set_ant_switch(sx127x_mode_t mode);
- [ ] sx127x_set_fifo_addr_ptr(uint8_t adr);
- [ ] sx127x_enter_rx_mode(void);
- [ ] sx127x_enter_tx_mode(void);
- [ ] sx127x_write_fifo(uint8_t *data, uint8_t len);
- [ ] sx127x_read_fifo(uint8_t *data, uint8_t *len);
- [ ] sx127x_set_tx_interrupt(void);
- [ ] sx127x_set_rx_interrupt(void);
- [ ] sx127x_read_reg(uint8_t adr, uint8_t *val);
- [ ] sx127x_write_reg(uint8_t adr, uint8_t val);
- [ ] sx127x_burst_read(uint8_t adr, uint8_t *ptr, uint8_t len);
- [ ] sx127x_burst_write(uint8_t adr, uint8_t *ptr, uint8_t len);
- [ ] sx127x_spi_init(void);
- [ ] sx127x_spi_transfer(uint8_t *wd, uint8_t *rd, uint16_t len);
- [ ] sx127x_spi_write_byte(uint8_t byte);
- [ ] sx127x_spi_write(uint8_t *data, uint16_t len);
- [ ] sx127x_spi_read(uint8_t *data, uint16_t len);
- [ ] sx127x_gpio_init(void);
- [ ] sx127X_gpio_write_reset(bool state);
- [ ] sx127x_gpio_read_nirq(void);
- [ ] sx127x_delay_ms(uint32_t ms);

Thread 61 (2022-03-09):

Firmware: Develop the RX of the UART driver

mgm8, 2022-03-09:
The current implementation only handle transmissions. As one interface of the TTC is a complete UART port, the RX part of the driver must be developed:
* The [DriverLib](https://github.com/spacelab-ufsc/ttc2/tree/dev_firmware/firmware/hal) must be used to handle the internal registers of the uC;
* The reception must be implemented using interruption;
* The incoming data must be stored in an internal buffer (a fixed size buffer);
* There must be a function to access the data available in the internal buffer (from an external device or task).

miguelboing, 2022-05-01:
**Uart Battery Test:**

1. Initialize uart (uart_init). Check the buffer initialization;
2. Enable RX interruption (uart_rx_enable);
3. Check interruption routine. See if the flags are being cleared correctly, byte is stored. Check second interruption or more interruptions;
4. Check available bytes (uart_read_available), see if they match with item 3;
5. Read buffer (uart_read) using available bytes from (uart_read_available);
6. Fill the buffer to cause overflow;
7. Clear the buffer (uart_flush). Check buffer content, head, tail, size, mtu;
8. Disable RX interruption (uart_rx_disable). Check if it is disabled sending data to the uC;
9. Enable RX again. Check if it is working using item 3.

Closed 2022-05-03.

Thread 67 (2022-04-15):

Firmware: Fix the unit test of the watchdog device

mgm8, 2022-04-15:
Currently the unit test of the watchdog device is failing, as can be seen [here](https://github.com/spacelab-ufsc/ttc2/runs/5975899546?check_suite_focus=true). As this test was imported from the OBDH 2.0 repository, the test should be updated for the TTC device implementation, by removing the use of the TPS382x peripheral (the TTC 2.0 module does not have an external watchdog IC).

Closed 2022-04-23.

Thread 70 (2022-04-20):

Firmware: Fix the unit test of the antenna device

mgm8, 2022-04-20:
Currently the unit test of the antenna device is failing, as can be seen [here](https://github.com/spacelab-ufsc/ttc2/runs/6096126518?check_suite_focus=true). As this test was imported from the OBDH 2.0 repository, the test should be updated for the TTC device implementation.

Closed 2022-05-03.

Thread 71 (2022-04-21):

Firmware: Fix the unit test of the media device

mgm8, 2022-04-21:
Currently the unit test of the media device is failing, as can be seen [here](https://github.com/spacelab-ufsc/ttc2/runs/6096126167?check_suite_focus=true). As this test was imported from the OBDH 2.0 repository, the test should be updated for the TTC device implementation.

Closed 2024-10-03.

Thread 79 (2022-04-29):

Firmware: Develop the Slave of the SPI driver

miguelboing, 2022-04-29:

mgm8, 2022-04-30:
[This issue already exists!](https://github.com/spacelab-ufsc/ttc2/issues/58)

Closed 2022-04-30.

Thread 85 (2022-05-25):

Firmware: Develop an ISR driver

mgm8, 2022-05-25:
As we have multiple drivers using interruption, a dedicated ISR driver will be required to avoid conflicts between different interruption routines.

Closed 2022-11-04.

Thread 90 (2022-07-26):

Firmware: Create a CONFIG_DEVs in startup.c for enabling devices initialization

joaoclaudioeb, 2022-07-26:
Create something like this:

```
#if defined(CONFIG_DEV_LEDS_ENABLED) && (CONFIG_DEV_LEDS_ENABLED == 1)
    /* LEDs device initialization */
    if (leds_init() != 0)
    {
        error_counter++;
    }
#endif /* CONFIG_DEV_LEDS_ENABLED */
```

Today is like this:

```
    /* LEDs device initialization */
    if (leds_init() != 0)
    {
        error_counter++;
    }
```

Closed 2022-11-04.

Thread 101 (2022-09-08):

Firmware: Fix Antenna failing initialization during boot.

miguelboing, 2022-09-08:

miguelboing, 2022-09-08:
Maybe we could use flags for tests to avoid having this error.

Closed 2023-11-06.

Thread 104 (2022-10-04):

Firmware: Fix external watchdog bug

miguelboing, 2022-10-04:
Currently the external watchdog tps382x is presenting unwanted behavior in the TTC board causing unexpected resets.

Closed 2022-11-04.

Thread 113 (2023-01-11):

Hardware: Fix the label of the "Fault" and "System" LEDs

mgm8, 2023-01-11:
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

miguelboing, 2024-10-03:
This issue was solved through a firmware gpio inversion.

Closed 2024-10-03.

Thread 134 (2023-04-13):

Firmware: Add a semaphore to access the radio module

mgm8, 2023-04-13:
As multiple tasks are using the radio module, a semaphore must be included to avoid more than one task using the radio at the same time. This should be done at the driver level.

Closed 2024-09-13.

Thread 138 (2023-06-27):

Firmware: Import the antenna deployment task from OBDH

miguelboing, 2023-06-27:
The TTC needs a task to initialize the antenna as a redundancy feature for OBDH. To avoid conflicts, the TTC tasks need to be delayed until after the OBDH antenna initialization.

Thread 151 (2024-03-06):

Firmware: Fix the DMA desynchronization after buffer position reset

miguelboing, 2024-03-06:

Closed 2024-09-13.

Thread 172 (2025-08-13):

Firmware: When a packet decoding error occurs, the radio transceiver stop working and the power consumption stuck at the maximum value

mgm8, 2025-08-13:

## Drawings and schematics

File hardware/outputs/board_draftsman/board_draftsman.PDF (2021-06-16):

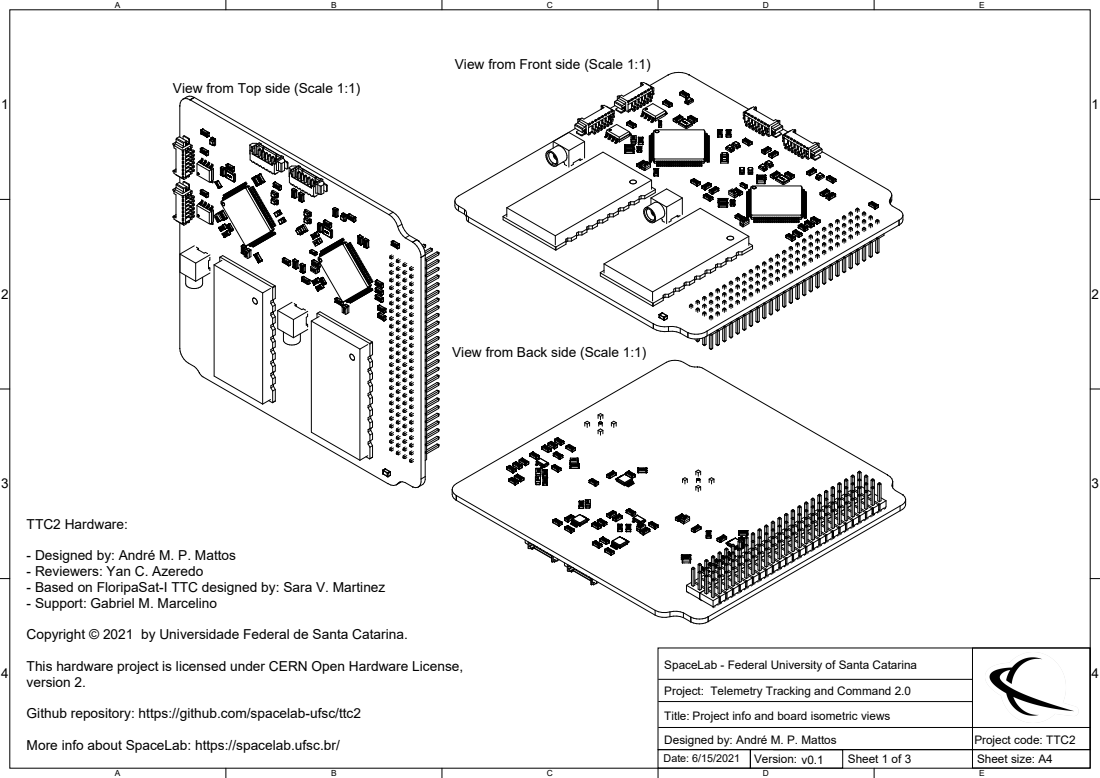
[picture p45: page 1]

View from Front side (Scale 1:1)

View from Top side (Scale 1:1)

View from Back side (Scale 1:1)

- Designed by: André M. P. Mattos
- Reviewers: Yan C. Azeredo
- Based on FloripaSat-I TTC designed by: Sara V. Martinez
- Support: Gabriel M. Marcelino

Copyright © 2021 by Universidade Federal de Santa Catarina.

This hardware project is licensed under CERN Open Hardware License,
version 2.

SpaceLab - Federal University of Santa Catarina

Telemetry Tracking and Command 2.0

Github repository: https://github.com/spacelab-ufsc/ttc2

Project info and board isometric views
Title:
Designed by: André M. P. Mattos

More info about SpaceLab: https://spacelab.ufsc.br/

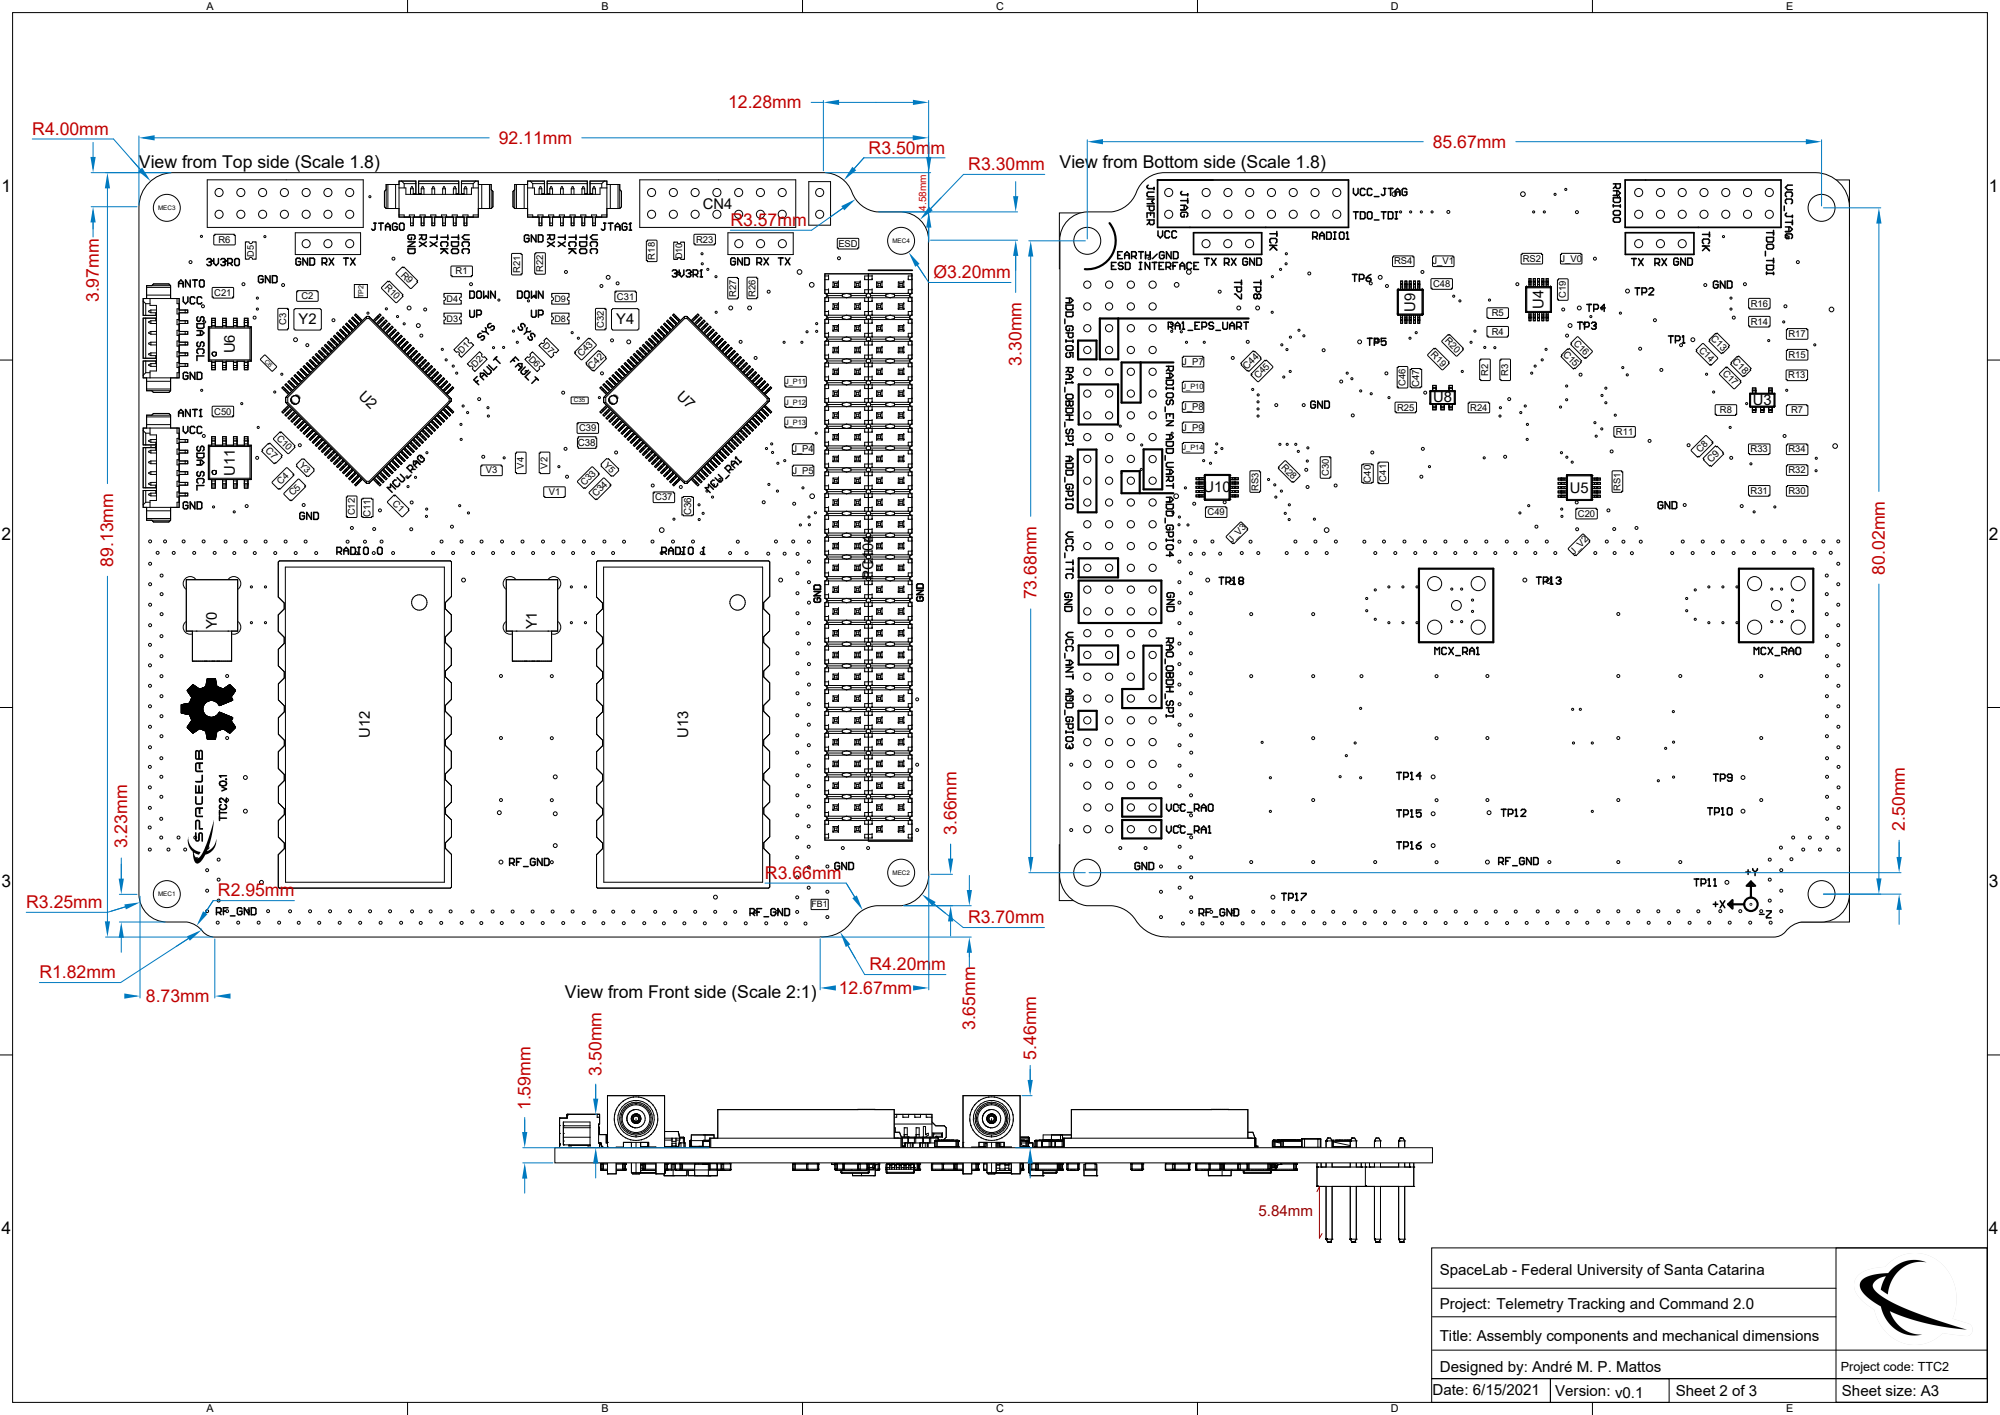
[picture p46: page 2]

View from Top side (Scale 1.8)

View from Bottom side (Scale 1.8)

View from Front side (Scale 2:1)

SpaceLab - Federal University of Santa Catarina

Telemetry Tracking and Command 2.0

Title: Assembly components and mechanical dimensions

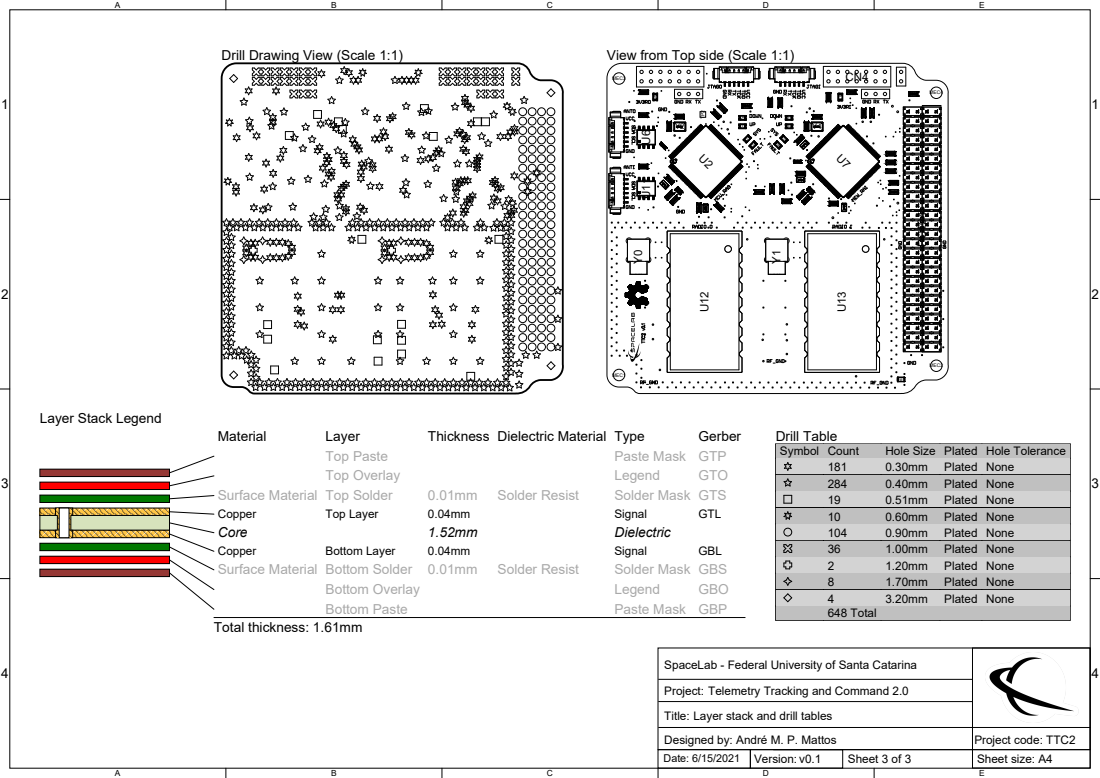
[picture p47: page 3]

Drill Drawing View (Scale 1:1)

View from Top side (Scale 1:1)

Symbol | Count | Hole Size | Plated | Hole Tolerance

181 | 0.30mm | Plated | None
284 | 0.40mm | Plated | None
19 | 0.51mm | Plated | None
10 | 0.60mm | Plated | None
104 | 0.90mm | Plated | None
36 | 1.00mm | Plated | None
2 | 1.20mm | Plated | None
8 | 1.70mm | Plated | None
4 | 3.20mm | Plated | None
648 Total

SpaceLab - Federal University of Santa Catarina

Project:
Layer stack and drill tables
Title:

Telemetry Tracking and Command 2.0

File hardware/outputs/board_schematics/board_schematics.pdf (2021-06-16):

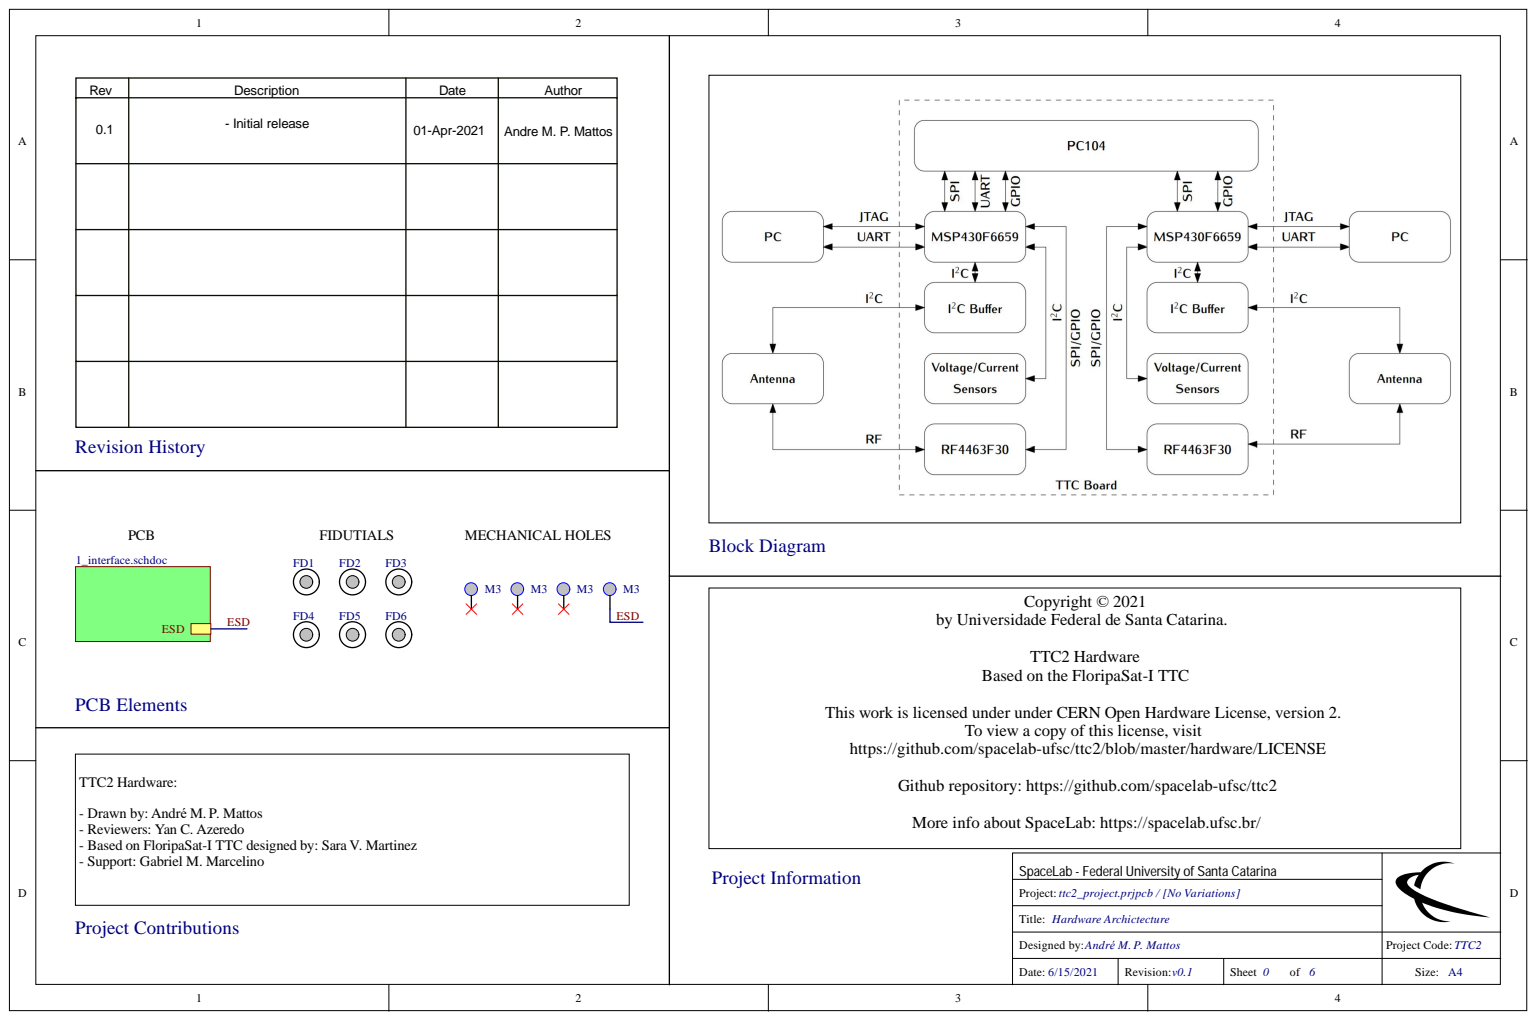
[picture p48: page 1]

R e v | D escri p t i o n | D a t e | Au t h o r

0 . 1 | | 0 1-Apr-2 0 2 1 | An dre M. P. Ma t t o

PCB Elements ESD 1_interface.schdoc PCB

Universidade Federal de Santa Catarina.

icensed under under CERN

To view a copy of
/spacelab-ufsc/

info about SpaceLab: ht

SpaceLab - Federal University of S

Des i g ned b y : A n d r é M. P. Ma t t o s | Project Co de: TTC2

Date: / / | Rev i s i o n : v0.1 | Sheet o f | Size: A

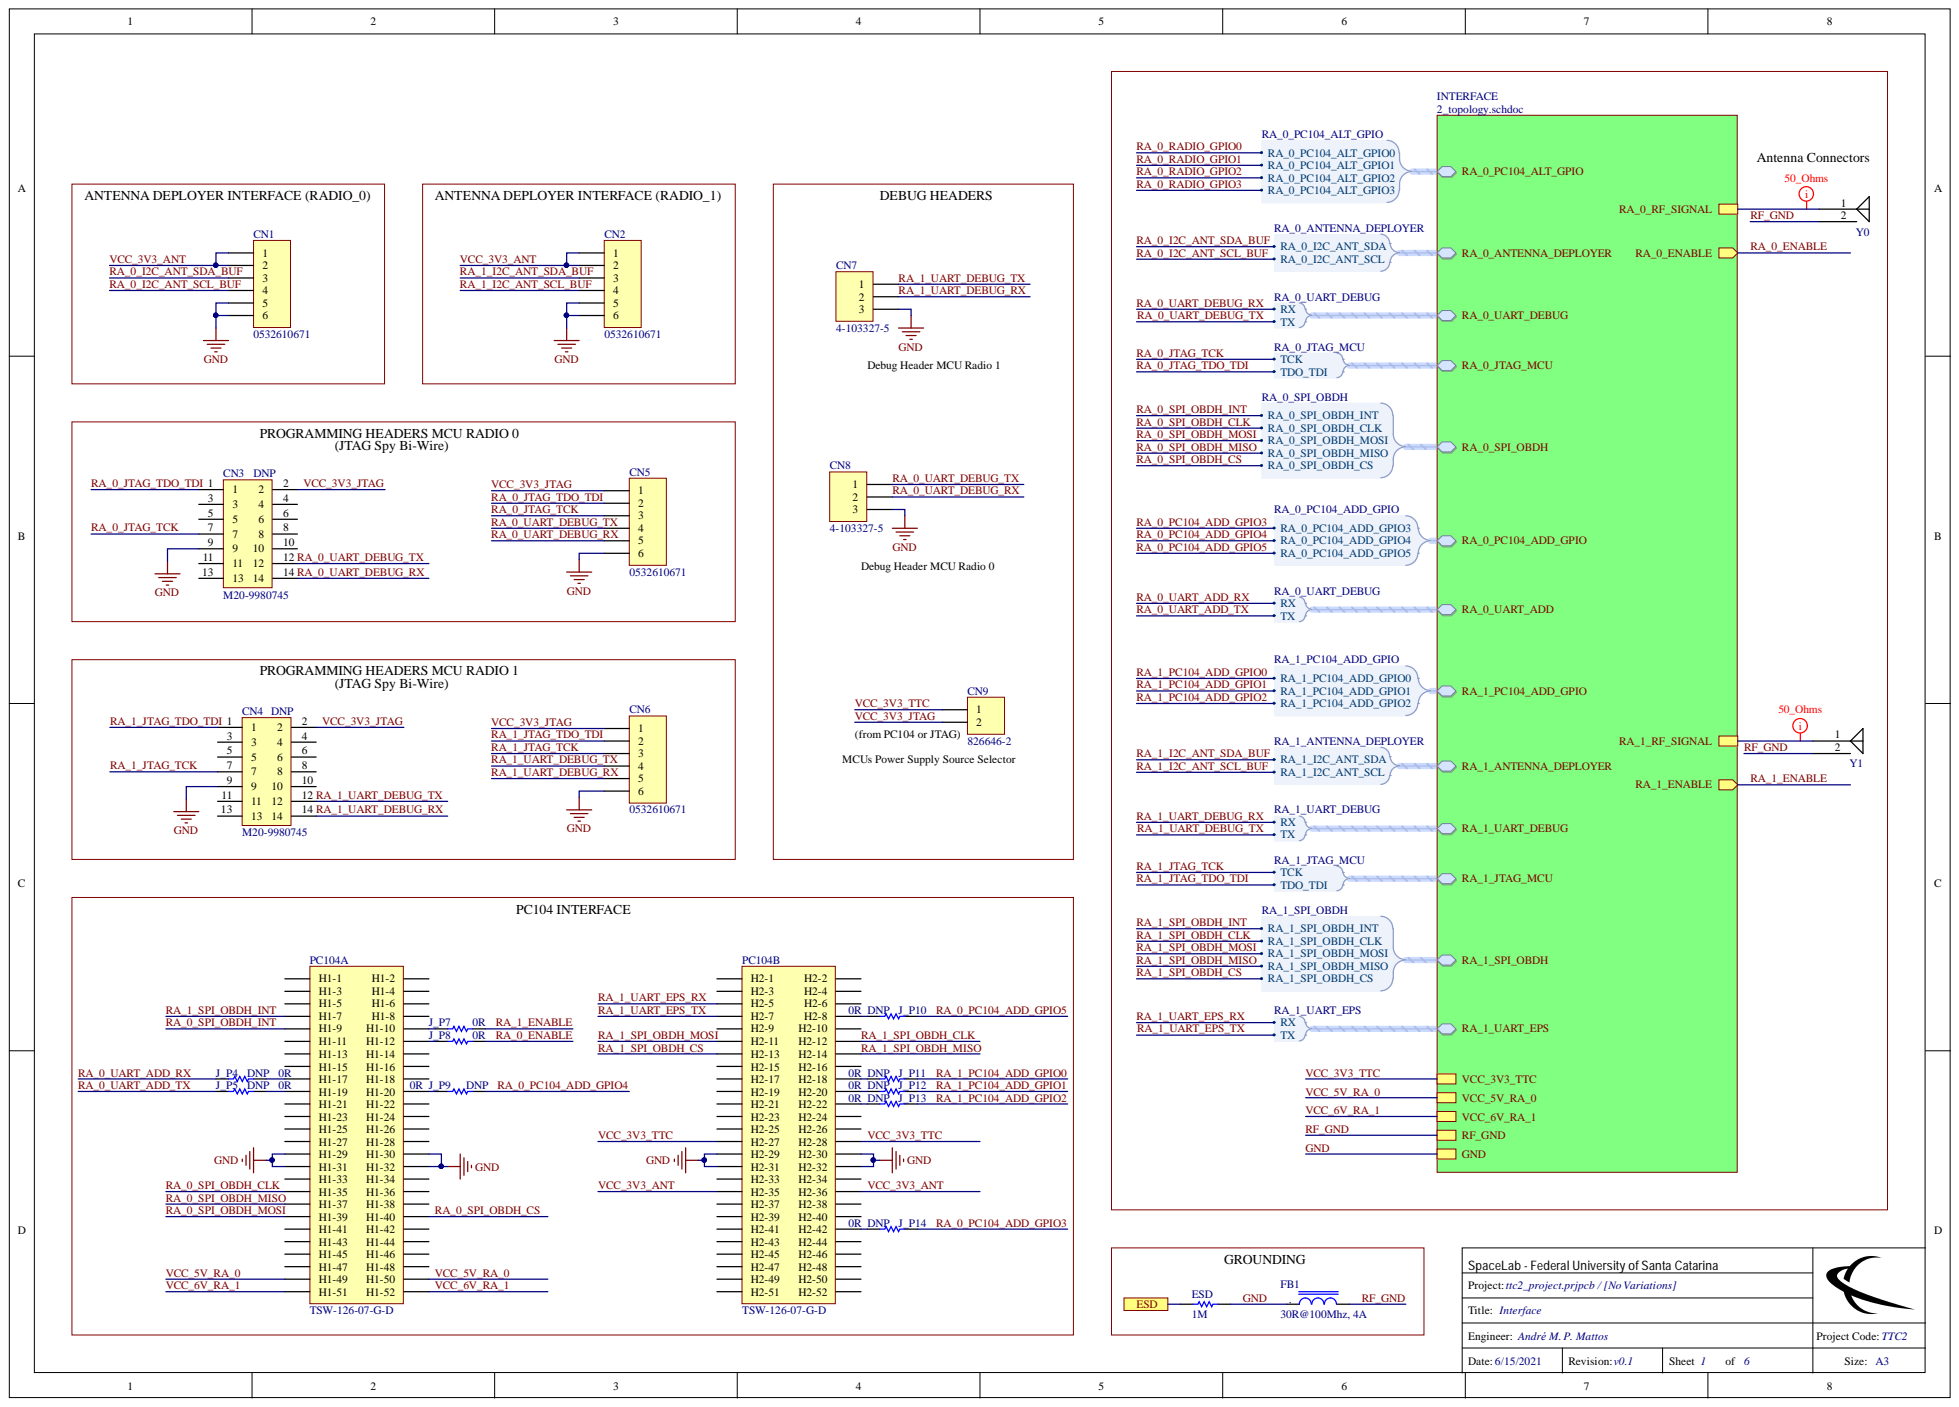
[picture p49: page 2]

GND
Debug Header MCU Radio 1

PROGRAMMING HEADERS MCU RADIO 0 (JTAG Spy Bi-Wire)

Debug Header MCU Radio 0

PROGRAMMING HEADERS MCU RADIO 1 (JTAG Spy Bi-Wire)

MCUs Power Supply Source Selector

SpaceLab - Federal University of Santa Catarina

Engineer: André M. P. Mattos | Project Code: TTC2

Date: | Revision: v0.1 | Sheet of 6 | Size: A3

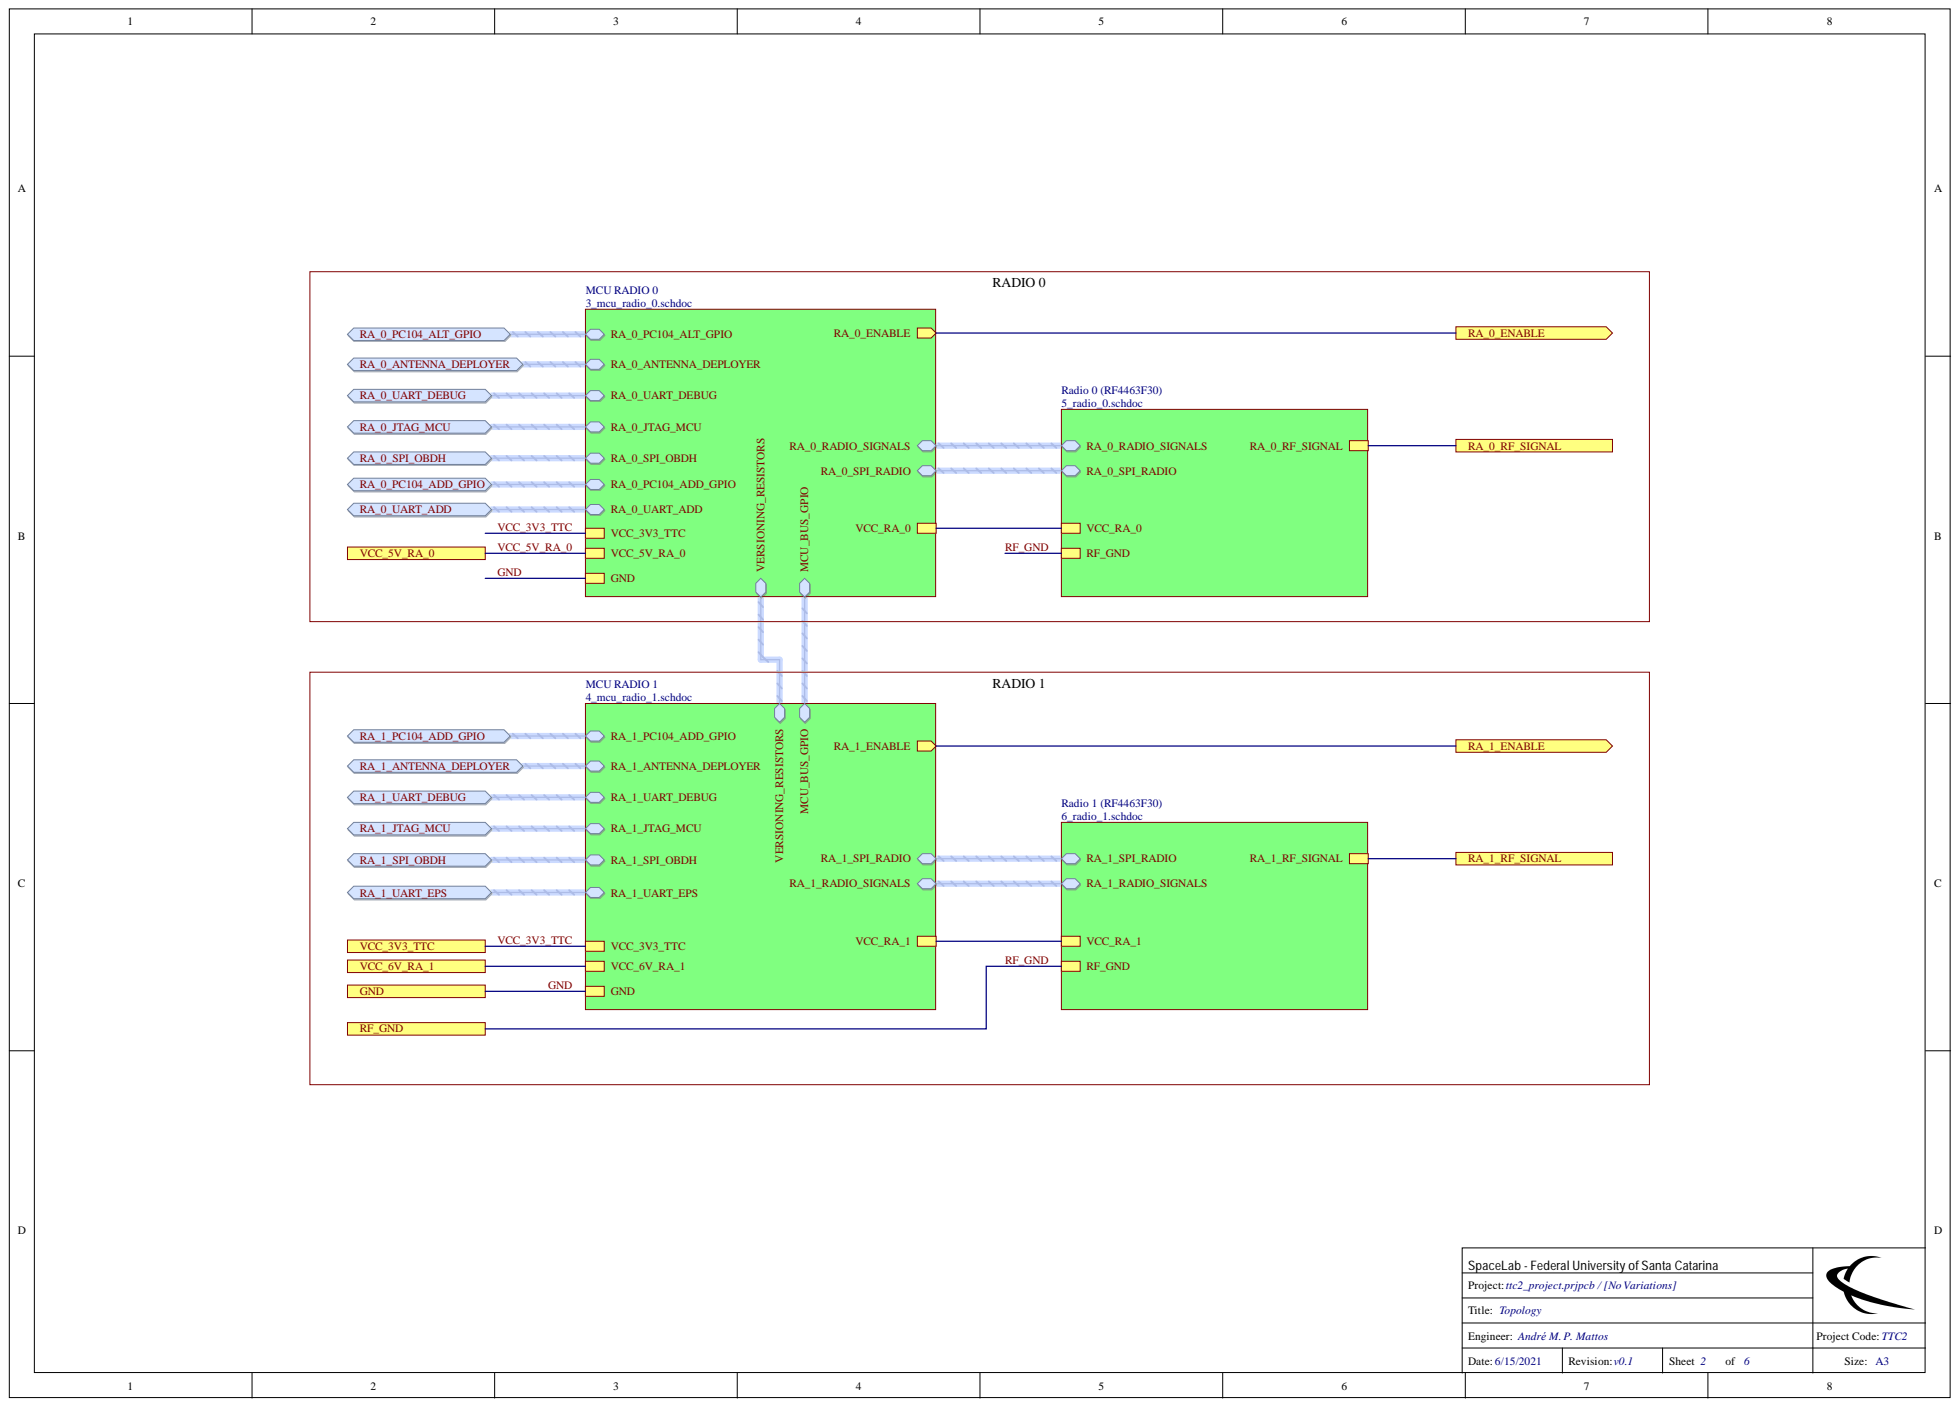
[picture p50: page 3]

VCC_6V_RA_1 | GND

SpaceLab - Federal University of Santa Catarina

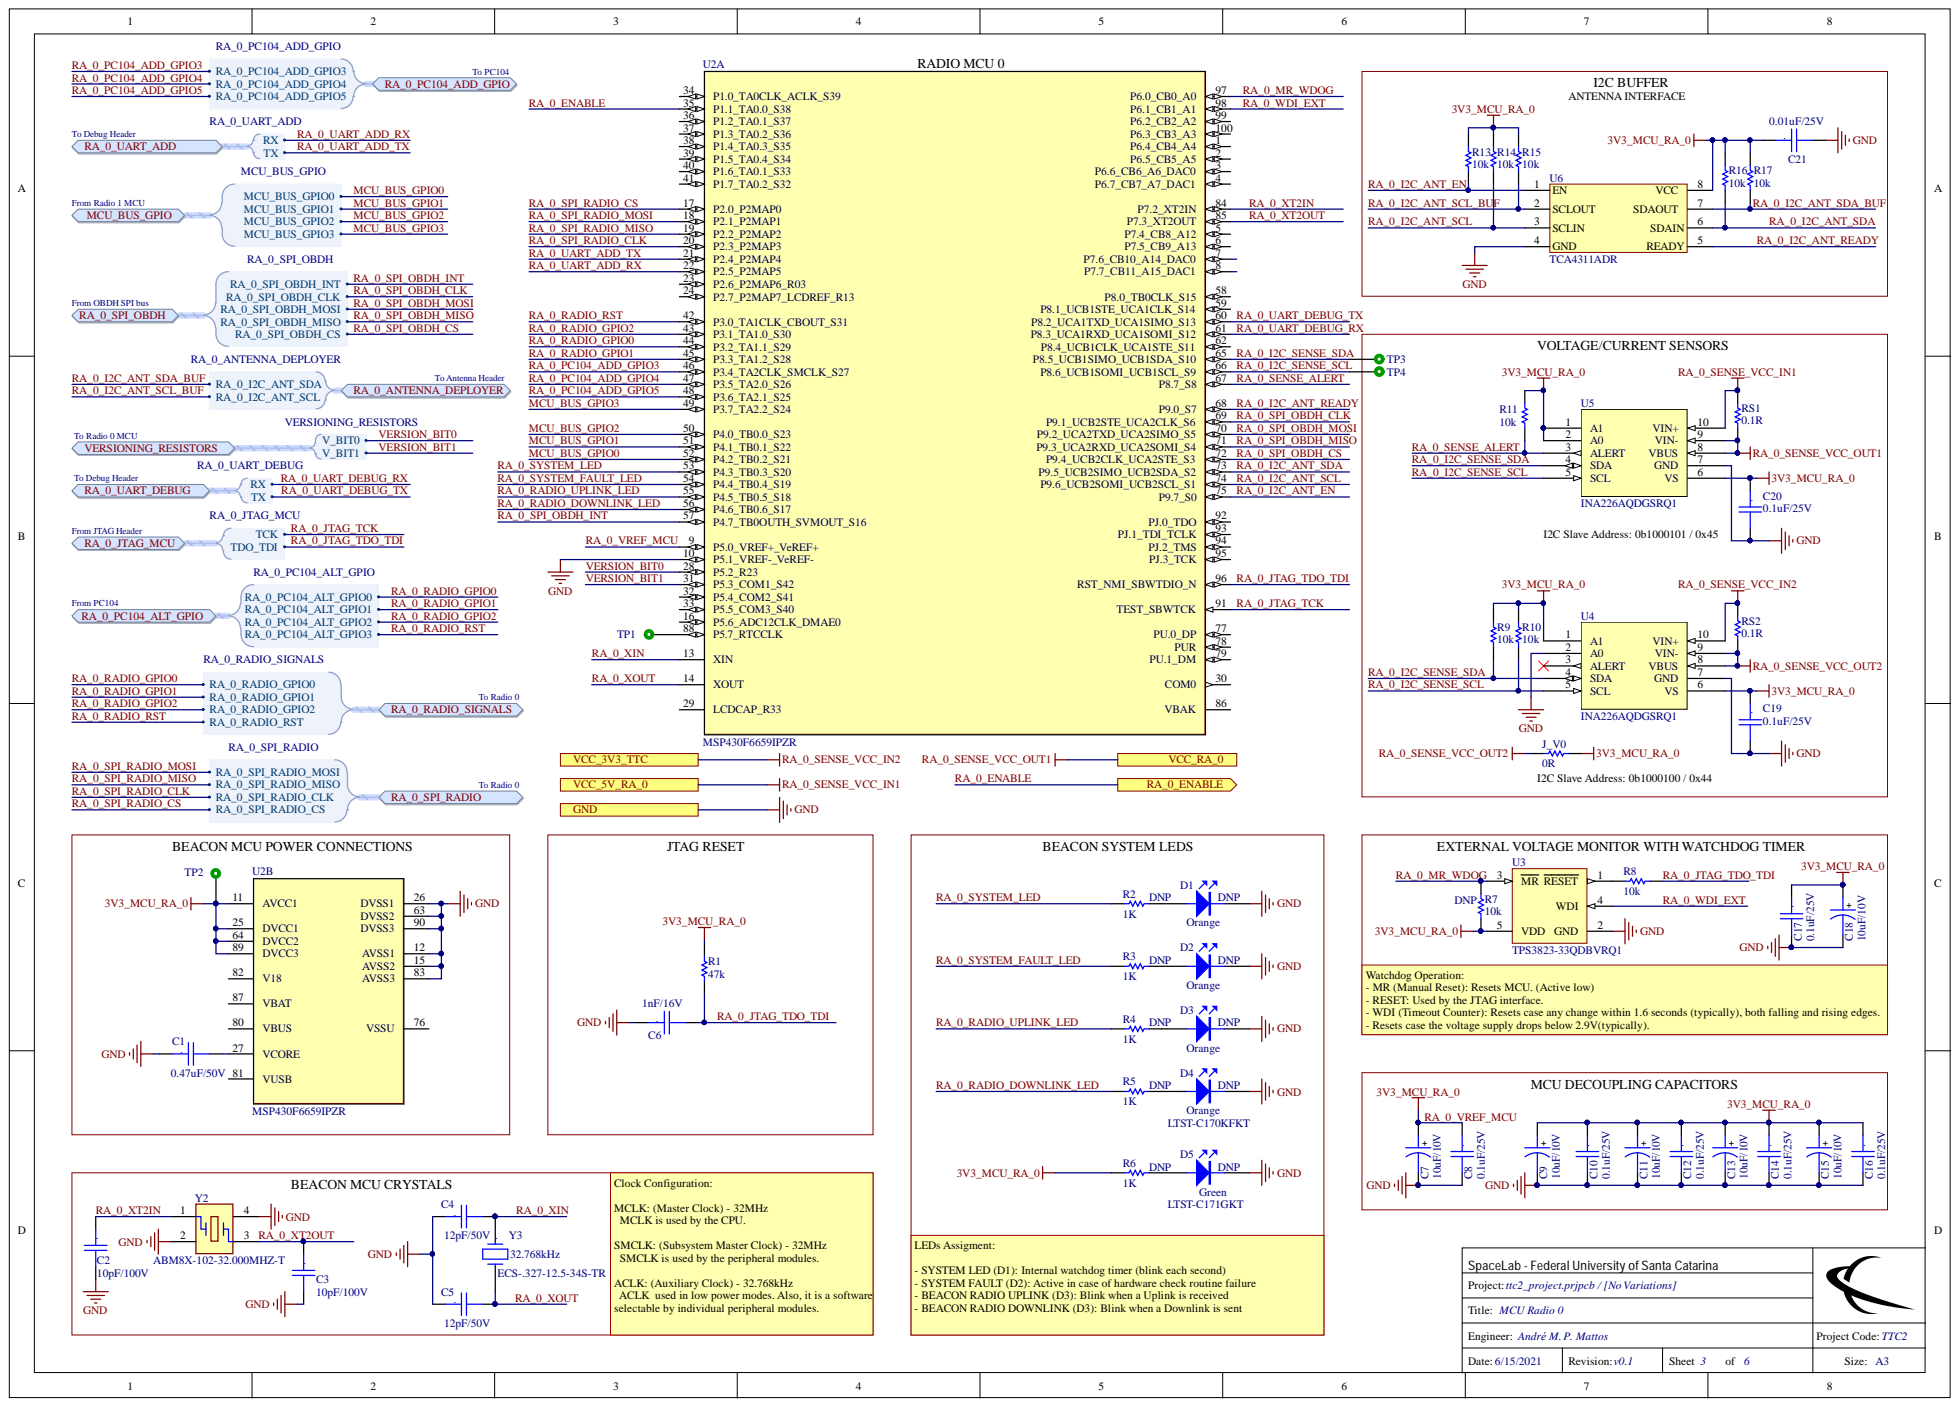
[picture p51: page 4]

RA_0_I2C_ANT_SCL_BUF | SCLOUT 2
RA_0_I2C_ANT_SCL | SCLIN 3

From OBDH SPI bus
RA_0_SPI_OBDH

ALERT 3

RA_0_I2C_SENSE_SCL

BEACON MCU POWER CONNECTIONS

EXTERNAL VOLTAGE MONITOR WITH WATCHDOG TIMER

Watchdog Operation:
- MR (Manual Reset): Resets MCU. (Active low)
- RESET: Used by the JTAG interface.
- WDI (Timeout Counter): Resets case any change within 1.6 seconds (typically), both falling and rising edges.
- Resets case the voltage supply drops below 2.9V(typically).

MCLK: (Master Clock) - 32MHz
MCLK is used by the CPU.

SMCLK: (Subsystem Master Clock) - 32MHz
SMCLK is used by the peripheral modules.

SpaceLab - Federal University of Santa Catarina

ACLK: (Auxiliary Clock) - 32.768kHz
ACLK used in low power modes. Also, it is a software
selectable by individual peripheral modules.

- SYSTEM LED (D1): Internal watchdog timer (blink each second)
- SYSTEM FAULT (D2): Active in case of hardware check routine failure
- BEACON RADIO UPLINK (D3): Blink when a Uplink is received
- BEACON RADIO DOWNLINK (D3): Blink when a Downlink is sent

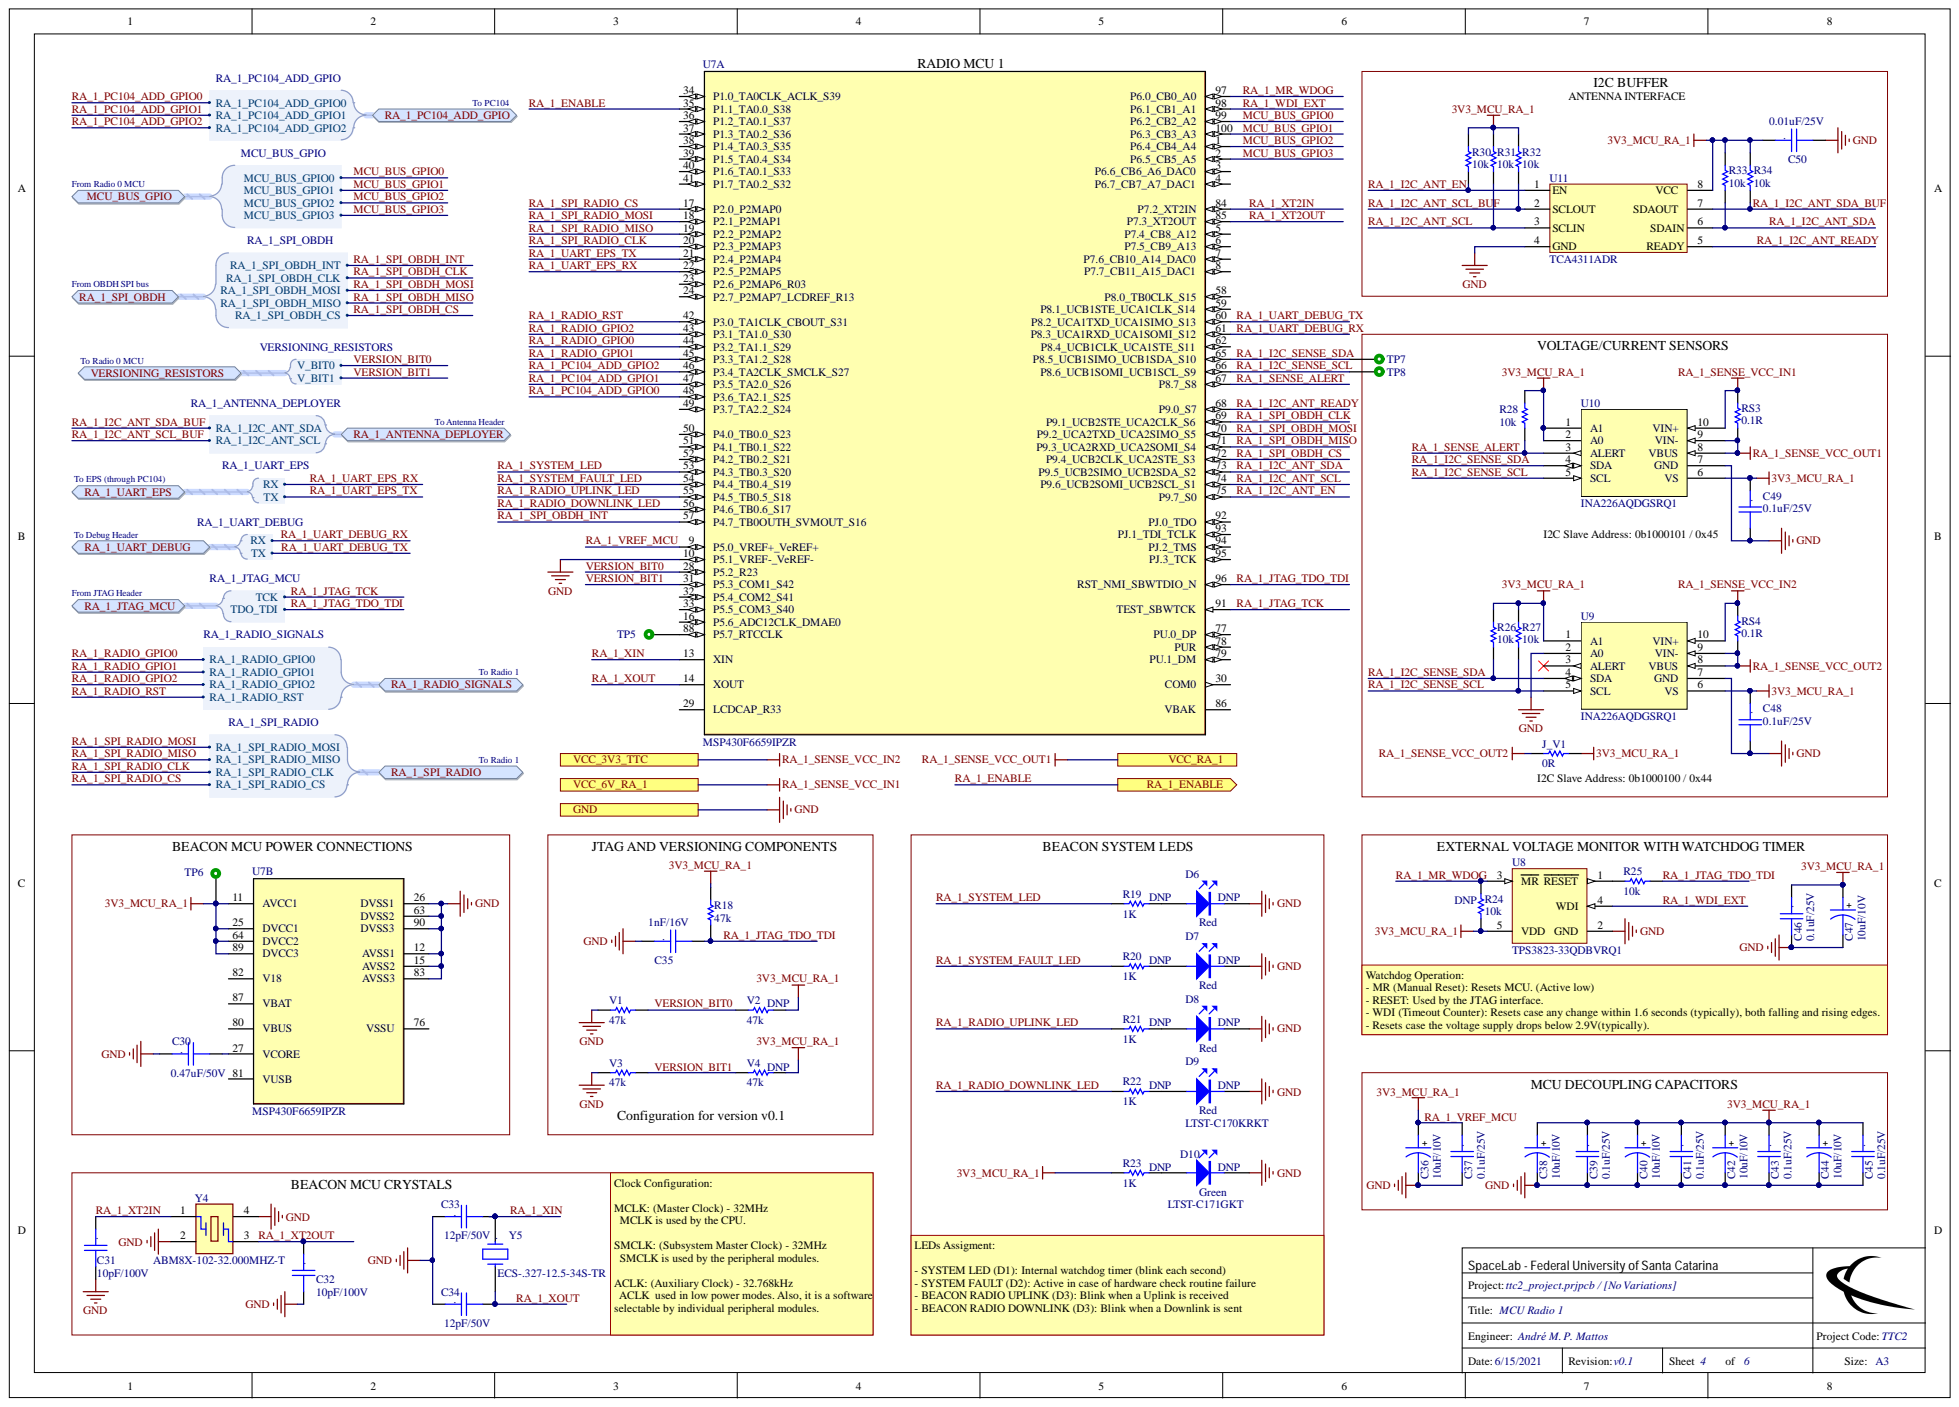
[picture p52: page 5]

RA_1_I2C_ANT_SCL_BUF | SCLOUT 2
RA_1_I2C_ANT_SCL | SCLIN 3

From OBDH SPI bus
RA_1_SPI_OBDH

BEACON MCU POWER CONNECTIONS

JTAG AND VERSIONING COMPONENTS

EXTERNAL VOLTAGE MONITOR WITH WATCHDOG TIMER

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

MCLK: (Master Clock) - 32MHz
MCLK is used by the CPU.

SMCLK: (Subsystem Master Clock) - 32MHz
SMCLK is used by the peripheral modules.

SpaceLab - Federal University of Santa Catarina

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

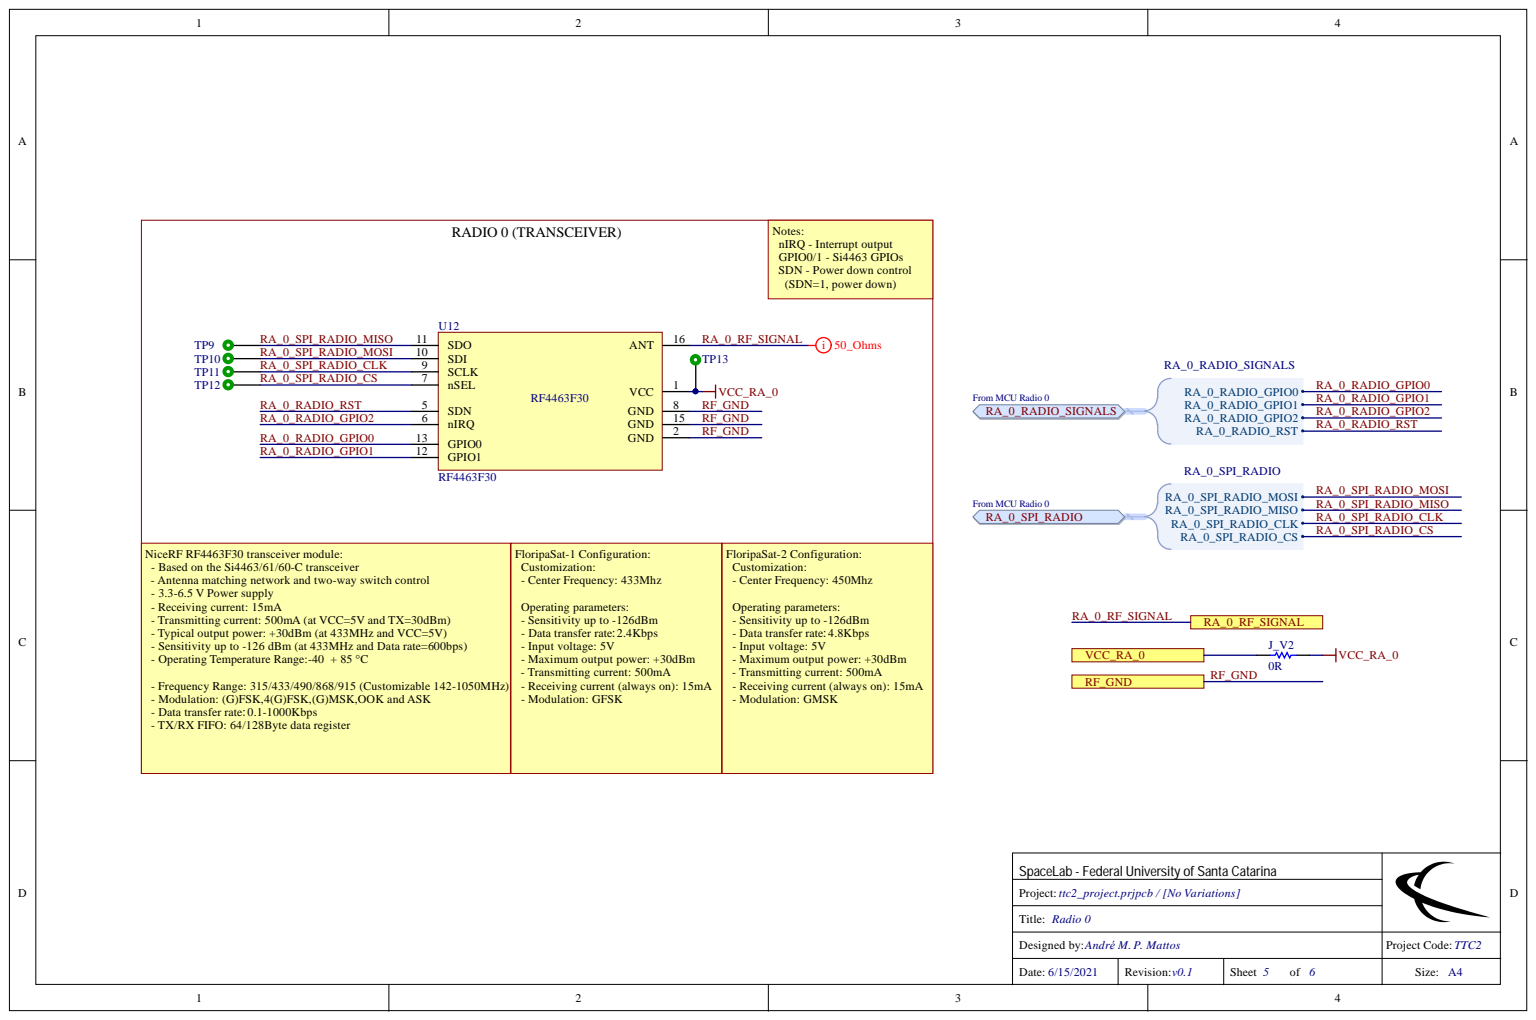
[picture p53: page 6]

Notes:
nIRQ - Interrupt output
GPIO0/1 - Si4463 GPIOs
SDN - Power down control
(SDN=1, power down)

NiceRF RF4463F30 transceiver module:
- Based on the Si4463/61/60-C transceiver
- Antenna matching network and two-way switch control
- 3.3-6.5 V Power supply
- Receiving current: 15mA
- Transmitting current: 500mA (at VCC=5V and TX=30dBm)
- Typical output power: +30dBm (at 433MHz and VCC=5V)
- Sensitivity up to -126 dBm (at 433MHz and Data rate=600bps)
- Operating Temperature Range:-40 + 85 °C

Operating parameters:
- Sensitivity up to -126dBm
- Data transfer rate：2.4Kbps
- Input voltage: 5V
- Maximum output power: +30dBm
- Transmitting current: 500mA
- Receiving current (always on): 15mA
- Modulation: GFSK

- Data transfer rate：4.8Kbps
- Modulation: GMSK

- Frequency Range: 315/433/490/868/915 (Customizable 142-1050MHz)
- Modulation: (G)FSK,4(G)FSK,(G)MSK,OOK and ASK
- Data transfer rate：0.1-1000Kbps
- TX/RX FIFO: 64/128Byte data register

SpaceLab - Federal University of Santa Catarina

Designed by: André M. P. Mattos | Project Code: TTC2

Date: | Revision: | Sheet of | Size: A4

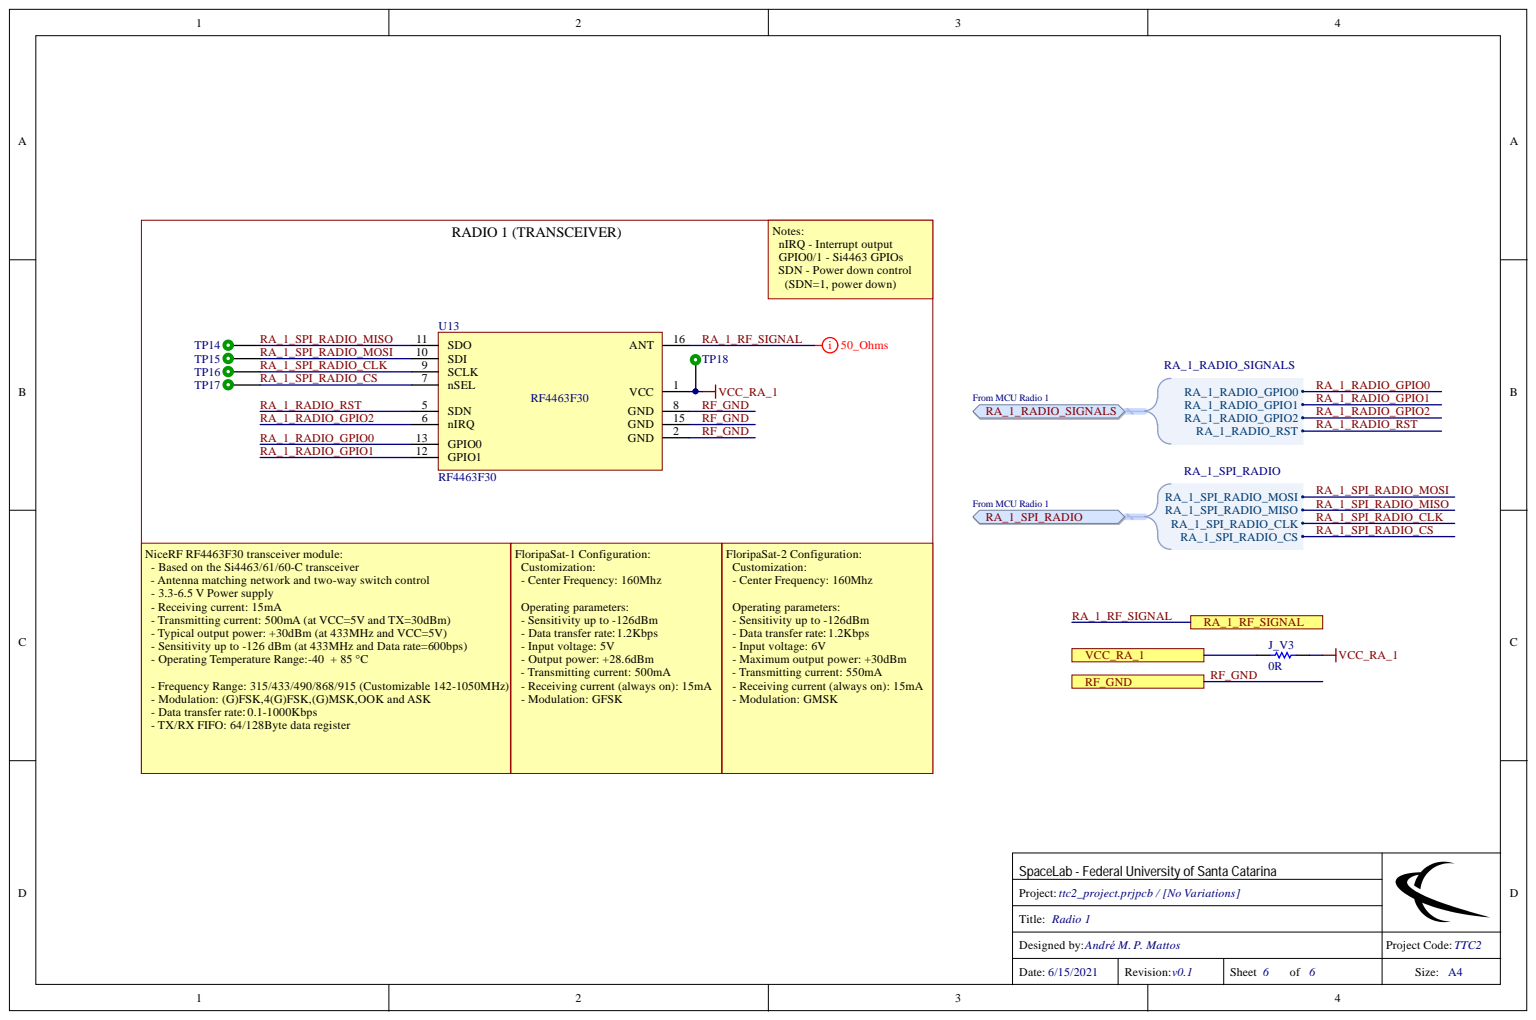
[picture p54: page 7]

Notes:
nIRQ - Interrupt output
GPIO0/1 - Si4463 GPIOs
SDN - Power down control
(SDN=1, power down)
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

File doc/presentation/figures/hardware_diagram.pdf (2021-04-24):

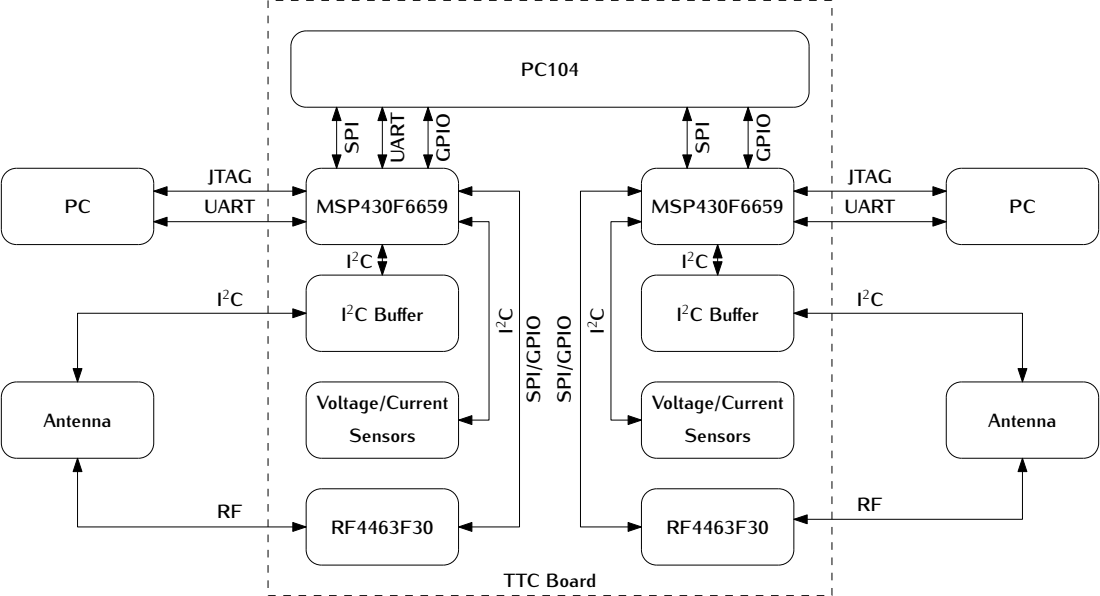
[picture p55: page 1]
MSP430F6659; Antenna RF Antenna PC; PC104 JTAG; TTC Board UART; 2C Buffer RF4463F30 SPI; UART; GPIO; 2C Buffer Voltage/Current Sensors; Voltage/Current Sensors RFI; PC JTAG UART SPI; GPIO SPI/GPIO SPI/GPIOI

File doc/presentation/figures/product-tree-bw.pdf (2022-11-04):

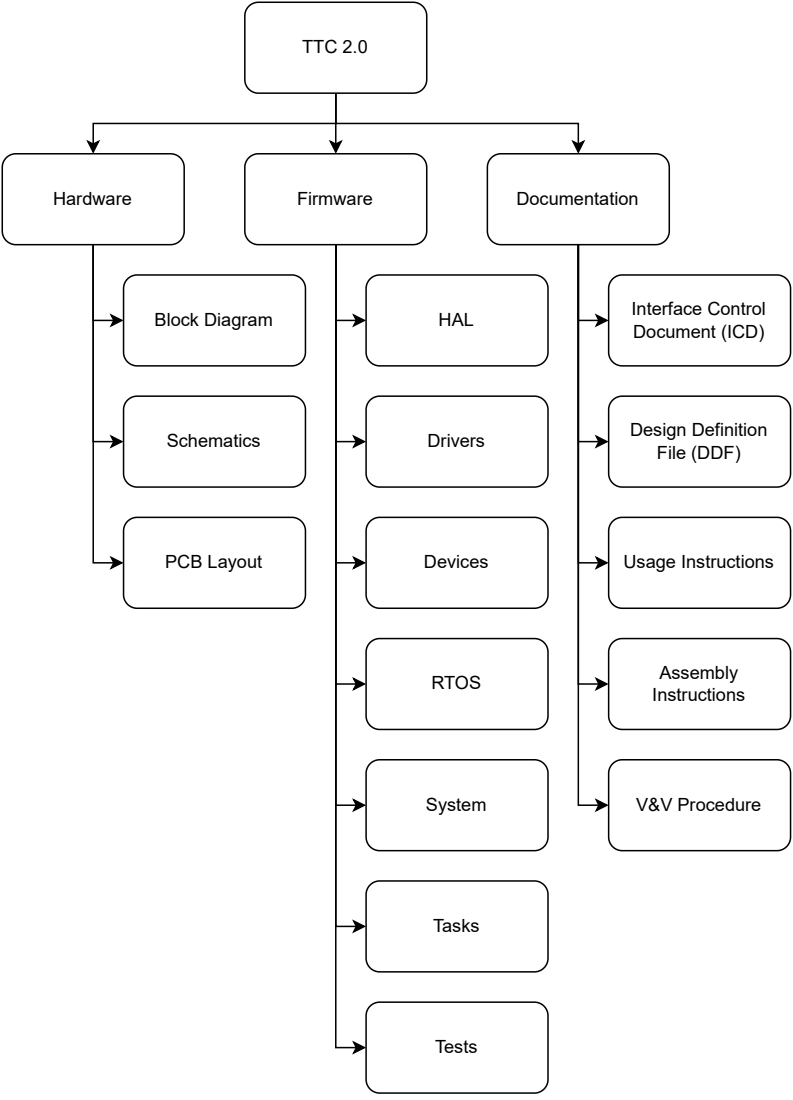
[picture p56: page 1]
TTC 2.0; Hardware; Firmware; Documentation; Interface Control Document (ICD); Design Definition File (DDF); Block Diagram; Schematics; PCB Layout; HAL; Drivers; Devices; RTOS; System; Tasks; Tests; Assembly Instructions; V&V Procedure; Usage Instructions

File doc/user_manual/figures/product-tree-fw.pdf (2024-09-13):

Drivers; Devices; Tasks; ADC; Flash; GPIO; INA22x; AntS; SPI (Master); SPI (Slave); TPS382x; WDT; UART; Antenna; Media; Power Sensor; Radio; Temperature Sensor; Watchdog; LED; Heartbeat; Radio Reset; Read Sensors; Startup; System Reset; Time Control; Uplink Manager; Downlink Manager; TTC 2.0 Firmware; RTOS; Tests; FreeRTOS; HAL; DriverLib; System; Clocks; Hooks; Setup; Log; Mockups; Libraries; Containers; NGHam; OBDH Server; EPS Server; Watchdog Reset; OBDH; EPS

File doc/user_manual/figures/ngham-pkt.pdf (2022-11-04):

Preamble 4 bytes; Sync Word 4 bytes; Size Tag 3 bytes; Header 1 byte; Payload 1-220 bytes; CRC 2 bytes; Padding 0-31 bytes; Parity Data 16 or 32 bytes

RS(255, 223) Code Block
RS(223, 191) Code Block
RS(191, 159) Code Block
RS(159, 127) Code Block
RS(111, 95) Code Block
RS(79, 63) Code Block
RS(47, 31) Code Block

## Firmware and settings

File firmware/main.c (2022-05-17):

/*
 * main.c
 * 
 * Copyright (C) 2021, SpaceLab.
 * 
 * This file is part of TTC 2.0.
 * 
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
 */

/**
 * \brief Main file.
 * 
 * \author Gabriel Mariano Marcelino <gabriel.mm8@gmail.com>
 * 
 * \version 0.1.9
 * 
 * \date 2021/04/04
 * 
 * \defgroup main Main file
 * \{
 */

#include <FreeRTOS.h>
#include <task.h>

#include "devices/watchdog/watchdog.h"
#include "system/clocks.h"
#include "app/tasks/tasks.h"

void main(void)
{
    /* Watchdog device initialization */
    int err = watchdog_init();

    /* System clocks configuration */
    clocks_config_t clk_conf = {0};

    clk_conf.mclk_hz    = 32000000UL;
    clk_conf.smclk_hz   = 32000000UL;
    clk_conf.aclk_hz    = 32768;

    err = clocks_setup(clk_conf);

    /* Create all the tasks */
    create_tasks();

    /* Start the scheduler */
    vTaskStartScheduler();

    /* Will only get here if there was insufficient memory to create the idle and/or timer task */
    while(1)
    {
    }
}

/** \} End of main group */

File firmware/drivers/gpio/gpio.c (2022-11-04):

/*
 * gpio.c
 * 
 * Copyright The TTC 2.0 Contributors.
 * 
 * This file is part of TTC 2.0.
 * 
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
 */

/**
 * \brief GPIO driver implementation.
 * 
 * \author Gabriel Mariano Marcelino <gabriel.mm8@gmail.com>
 * 
 * \version 0.3.0
 * 
 * \date 2020/01/13
 * 
 * \addtogroup gpio
 * \{
 */

#include <hal/gpio.h>

#include <config/config.h>
#include <system/sys_log/sys_log.h>

#include "gpio.h"

static const uint16_t GPIO_PORT_TO_BASE[] = { // cppcheck-suppress misra-c2012-8.9
    0x00,
#if defined(__MSP430_HAS_PORT1_R__)
    __MSP430_BASEADDRESS_PORT1_R__,
#elif defined(__MSP430_HAS_PORT1__)
    __MSP430_BASEADDRESS_PORT1__,
#else
    0xFFFF,
#endif
#if defined(__MSP430_HAS_PORT2_R__)
    __MSP430_BASEADDRESS_PORT2_R__,
#elif defined(__MSP430_HAS_PORT2__)
    __MSP430_BASEADDRESS_PORT2__,
#else
    0xFFFF,
#endif
#if defined(__MSP430_HAS_PORT3_R__)
    __MSP430_BASEADDRESS_PORT3_R__,
#elif defined(__MSP430_HAS_PORT3__)
    __MSP430_BASEADDRESS_PORT3__,
#else
    0xFFFF,
#endif
#if defined(__MSP430_HAS_PORT4_R__)
    __MSP430_BASEADDRESS_PORT4_R__,
#elif defined(__MSP430_HAS_PORT4__)
    __MSP430_BASEADDRESS_PORT4__,
#else
    0xFFFF,
#endif
#if defined(__MSP430_HAS_PORT5_R__)
    __MSP430_BASEADDRESS_PORT5_R__,
#elif defined(__MSP430_HAS_PORT5__)
    __MSP430_BASEADDRESS_PORT5__,
#else
    0xFFFF,
#endif
#if defined(__MSP430_HAS_PORT6_R__)
    __MSP430_BASEADDRESS_PORT6_R__,
#elif defined(__MSP430_HAS_PORT6__)
    __MSP430_BASEADDRESS_PORT6__,
#else
    0xFFFF,
#endif
#if defined(__MSP430_HAS_PORT7_R__)
    __MSP430_BASEADDRESS_PORT7_R__,
#elif defined(__MSP430_HAS_PORT7__)
    __MSP430_BASEADDRESS_PORT7__,
#else
    0xFFFF,
#endif
#if defined(__MSP430_HAS_PORT8_R__)
    __MSP430_BASEADDRESS_PORT8_R__,
#elif defined(__MSP430_HAS_PORT8__)
    __MSP430_BASEADDRESS_PORT8__,
#else
    0xFFFF,
#endif
#if defined(__MSP430_HAS_PORT9_R__)
    __MSP430_BASEADDRESS_PORT9_R__,
#elif defined(__MSP430_HAS_PORT9__)
    __MSP430_BASEADDRESS_PORT9__,
#else
    0xFFFF,
#endif
#if defined(__MSP430_HAS_PORT10_R__)
    __MSP430_BASEADDRESS_PORT10_R__,
#elif defined(__MSP430_HAS_PORT10__)
    __MSP430_BASEADDRESS_PORT10__,
#else
    0xFFFF,
#endif
#if defined(__MSP430_HAS_PORT11_R__)
    __MSP430_BASEADDRESS_PORT11_R__,
#elif defined(__MSP430_HAS_PORT11__)
    __MSP430_BASEADDRESS_PORT11__,
#else
    0xFFFF,
#endif
    0xFFFF,
#if defined(__MSP430_HAS_PORTJ_R__)
    __MSP430_BASEADDRESS_PORTJ_R__
#elif defined(__MSP430_HAS_PORTJ__)
    __MSP430_BASEADDRESS_PORTJ__
#else
    0xFFFF
#endif
};

int gpio_init(gpio_pin_t pin, gpio_config_t config)
{
    int err = 0;

    uint8_t msp_port = UINT8_MAX;
    uint16_t msp_pin = UINT16_MAX;
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

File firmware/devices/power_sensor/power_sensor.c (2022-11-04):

/*
 * power_sensor.c
 * 
 * Copyright The TTC 2.0 Contributors.
 * 
 * This file is part of TTC 2.0.
 * 
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
 */

/**
 * \brief Power sensor device implementation.
 * 
 * \author Gabriel Mariano Marcelino <gabriel.mm8@gmail.com>
 * \author Miguel Boing <miguelboing13@gmail.com>
 * 
 * \version 0.2.5
 * 
 * \date 2021/04/11
 * 
 * \addtogroup power_sensor
 * \{
 */

#include <system/sys_log/sys_log.h>

#include <drivers/ina22x/ina22x.h>

#include "power_sensor.h"

static ina22x_config_t uc_config = {
    .i2c_port                   = I2C_PORT_1,
    .i2c_conf.speed_hz          = 100000,
    .i2c_adr                    = 0x44,
    .avg_mode                   = INA22X_AVERAGING_MODE_128,
    .bus_voltage_conv_time      = INA22X_BUS_VOLTAGE_CONV_TIME_588u,
    .shunt_voltage_conv_time    = INA22X_SHUNT_VOLTAGE_CONV_TIME_588u,
    .op_mode                    = INA22X_MODE_SHUNT_BUS_CONT,
    .lsb_current                = 5e-6,
    .cal                        = 10240,
};

static ina22x_config_t radio_config = {
    .i2c_port                   = I2C_PORT_1,
    .i2c_conf.speed_hz          = 100000,
    .i2c_adr                    = 0x45,
    .avg_mode                   = INA22X_AVERAGING_MODE_128,
    .bus_voltage_conv_time      = INA22X_BUS_VOLTAGE_CONV_TIME_588u,
    .shunt_voltage_conv_time    = INA22X_SHUNT_VOLTAGE_CONV_TIME_588u,
    .op_mode                    = INA22X_MODE_SHUNT_BUS_CONT,
    .lsb_current                = 5e-5,
    .cal                        = 1024,
};

/**
 * \brief Reads the voltage scaled from the power sensor.
 *
 * \param[in] device is the target sensor to be read.
 *
 * \param[in] shunt_scale is the SI scale for shunt voltage. It can be:
 * \parblock
 *     -\b POWER_SENSOR_MICRO_SCALE
 *     -\b POWER_SENSOR_MILI_SCALE
 *     .
 * \endparblock
 *
 * \param[in] bus_scale is the SI scale for bus voltage. It can be:
 * \parblock
 *     -\b POWER_SENSOR_MICRO_SCALE
 *     -\b POWER_SENSOR_MILI_SCALE
 *     .
 * \endparblock
 *
 * \param[in,out] volt_shunt is a pointer to store the read voltage scaled.
 *
 * \param[in,out] volt_bus is a pointer to store the read voltage scaled.
 *
 * \return The status/error code.
 */
static int power_sensor_read_voltage_scaled(power_sensor_measured_device_t device, power_sensor_scale_t shunt_scale, power_sensor_scale_t bus_scale, voltage_t *volt_shunt, voltage_t *volt_bus);

/**
 * \brief Reads the current scaled from the power sensor.
 *
 * \param[in] device is the target sensor to be read.
 *
 * \param[in,out] scale is the SI scale for shunt current. It can be:
 * \parblock
 *     -\b POWER_SENSOR_MICRO_SCALE
 *     -\b POWER_SENSOR_MILI_SCALE
 *     .
 * \endparblock
 *
 * \param[in,out] curr is a pointer to store the read current scaled.
 *
 * \return The status/error code.
 */
static int power_sensor_read_current_scaled(power_sensor_measured_device_t device, power_sensor_scale_t scale, current_t *curr);

/**
 * \brief Reads the power scaled from the power sensor.
 *
 * \param[in] device is the target sensor to be read.
 *
 * \param[in,out] scale is the SI scale for shunt power. It can be:
 * \parblock
 *     -\b POWER_SENSOR_MICRO_SCALE
 *     -\b POWER_SENSOR_MILI_SCALE
 *     .
 * \endparblock
 *
 * \param[in,out] pwr is a pointer to store the read power scaled.
 *
 * \return The status/error code.
 */
static int power_sensor_read_power_scaled(power_sensor_measured_device_t device, power_sensor_scale_t scale, power_t *pwr);

int power_sensor_init(void)
{
    int err = -1;

    sys_log_print_event_from_module(SYS_LOG_INFO, POWER_SENSOR_MODULE_NAME, "Initializing the power sensor...");
    sys_log_new_line();

    /* Power sensor initialization */
    if ((ina22x_init(radio_config) == 0) && (ina22x_init(uc_config) == 0))
    {
        /* Power sensor configuration */
        if ((ina22x_configuration(radio_config) == 0) && (ina22x_configuration(uc_config) == 0))
        {
            /* Power sensor calibration */
            if ((ina22x_calibration(radio_config) == 0) && (ina22x_calibration(uc_config) == 0))
            {
                err = 0;
            }
            else
            {
            #if defined(CONFIG_DRIVERS_DEBUG_ENABLED) && (CONFIG_DRIVERS_DEBUG_ENABLED == 1)
                sys_log_print_event_from_module(SYS_LOG_ERROR, POWER_SENSOR_MODULE_NAME, "Error during the initialization: Driver calibration has failed!");
                sys_log_new_line();
            #endif /* CONFIG_DRIVERS_DEBUG_ENABLED */
            }
        }
        else
        {
        #if defined(CONFIG_DRIVERS_DEBUG_ENABLED) && (CONFIG_DRIVERS_DEBUG_ENABLED == 1)
                sys_log_print_event_from_module(SYS_LOG_ERROR, POWER_SENSOR_MODULE_NAME, "Error during the initialization: Driver configuration has failed!");
                sys_log_new_line();
        #endif /* CONFIG_DRIVERS_DEBUG_ENABLED */
        }
    }
    else
    {
    #if defined(CONFIG_DRIVERS_DEBUG_ENABLED) && (CONFIG_DRIVERS_DEBUG_ENABLED == 1)
        sys_log_print_event_from_module(SYS_LOG_ERROR, POWER_SENSOR_MODULE_NAME, "Error during the initialization: Driver initialization has failed!");
        sys_log_new_line();
    #endif /* CONFIG_DRIVERS_DEBUG_ENABLED */
    }

    return err;
}
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

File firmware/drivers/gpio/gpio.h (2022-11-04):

/*
 * gpio.h
 * 
 * Copyright The TTC 2.0 Contributors.
 * 
 * This file is part of TTC 2.0.
 * 
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
 */

/**
 * \brief GPIO driver definition.
 * 
 * \author Gabriel Mariano Marcelino <gabriel.mm8@gmail.com>
 * 
 * \version 0.3.0
 * 
 * \date 2020/01/13
 * 
 * \defgroup gpio GPIO
 * \ingroup drivers
 * \{
 */

#ifndef GPIO_H_
#define GPIO_H_

#include <stdint.h>
#include <stdbool.h>

#define GPIO_MODULE_NAME    "GPIO"

/* Pin states */
#define GPIO_STATE_LOW      0
#define GPIO_STATE_HIGH     1

/**
 * \brief GPIO pins.
 */
typedef enum
{
    GPIO_PIN_0=0,           /**< GPIO pin 0. */
    GPIO_PIN_1,             /**< GPIO pin 1. */
    GPIO_PIN_2,             /**< GPIO pin 2. */
    GPIO_PIN_3,             /**< GPIO pin 3. */
    GPIO_PIN_4,             /**< GPIO pin 4. */
    GPIO_PIN_5,             /**< GPIO pin 5. */
    GPIO_PIN_6,             /**< GPIO pin 6. */
    GPIO_PIN_7,             /**< GPIO pin 7. */
    GPIO_PIN_8,             /**< GPIO pin 8. */
    GPIO_PIN_9,             /**< GPIO pin 9. */
    GPIO_PIN_10,            /**< GPIO pin 10. */
    GPIO_PIN_11,            /**< GPIO pin 11. */
    GPIO_PIN_12,            /**< GPIO pin 12. */
    GPIO_PIN_13,            /**< GPIO pin 13. */
    GPIO_PIN_14,            /**< GPIO pin 14. */
    GPIO_PIN_15,            /**< GPIO pin 15. */
    GPIO_PIN_16,            /**< GPIO pin 16. */
    GPIO_PIN_17,            /**< GPIO pin 17. */
    GPIO_PIN_18,            /**< GPIO pin 18. */
    GPIO_PIN_19,            /**< GPIO pin 19. */
    GPIO_PIN_20,            /**< GPIO pin 20. */
    GPIO_PIN_21,            /**< GPIO pin 21. */
    GPIO_PIN_22,            /**< GPIO pin 22. */
    GPIO_PIN_23,            /**< GPIO pin 23. */
    GPIO_PIN_24,            /**< GPIO pin 24. */
    GPIO_PIN_25,            /**< GPIO pin 25. */
    GPIO_PIN_26,            /**< GPIO pin 26. */
    GPIO_PIN_27,            /**< GPIO pin 27. */
    GPIO_PIN_28,            /**< GPIO pin 28. */
    GPIO_PIN_29,            /**< GPIO pin 29. */
    GPIO_PIN_30,            /**< GPIO pin 30. */
    GPIO_PIN_31,            /**< GPIO pin 31. */
    GPIO_PIN_32,            /**< GPIO pin 32. */
    GPIO_PIN_33,            /**< GPIO pin 33. */
    GPIO_PIN_34,            /**< GPIO pin 34. */
    GPIO_PIN_35,            /**< GPIO pin 35. */
    GPIO_PIN_36,            /**< GPIO pin 36. */
    GPIO_PIN_37,            /**< GPIO pin 37. */
    GPIO_PIN_38,            /**< GPIO pin 38. */
    GPIO_PIN_39,            /**< GPIO pin 39. */
    GPIO_PIN_40,            /**< GPIO pin 40. */
    GPIO_PIN_41,            /**< GPIO pin 41. */
    GPIO_PIN_42,            /**< GPIO pin 42. */
    GPIO_PIN_43,            /**< GPIO pin 43. */
    GPIO_PIN_44,            /**< GPIO pin 44. */
    GPIO_PIN_45,            /**< GPIO pin 45. */
    GPIO_PIN_46,            /**< GPIO pin 46. */
    GPIO_PIN_47,            /**< GPIO pin 47. */
    GPIO_PIN_48,            /**< GPIO pin 48. */
    GPIO_PIN_49,            /**< GPIO pin 49. */
    GPIO_PIN_50,            /**< GPIO pin 50. */
    GPIO_PIN_51,            /**< GPIO pin 51. */
    GPIO_PIN_52,            /**< GPIO pin 52. */
    GPIO_PIN_53,            /**< GPIO pin 53. */
    GPIO_PIN_54,            /**< GPIO pin 54. */
    GPIO_PIN_55,            /**< GPIO pin 55. */
    GPIO_PIN_56,            /**< GPIO pin 56. */
    GPIO_PIN_57,            /**< GPIO pin 57. */
    GPIO_PIN_58,            /**< GPIO pin 58. */
    GPIO_PIN_59,            /**< GPIO pin 59. */
    GPIO_PIN_60,            /**< GPIO pin 60. */
    GPIO_PIN_61,            /**< GPIO pin 61. */
    GPIO_PIN_62,            /**< GPIO pin 62. */
    GPIO_PIN_63,            /**< GPIO pin 63. */
    GPIO_PIN_64,            /**< GPIO pin 64. */
    GPIO_PIN_65,            /**< GPIO pin 65. */
    GPIO_PIN_66,            /**< GPIO pin 66. */
    GPIO_PIN_67,            /**< GPIO pin 67. */
    GPIO_PIN_68,            /**< GPIO pin 68. */
    GPIO_PIN_69             /**< GPIO pin 69. */
} gpio_pin_t;

/**
 * \brief GPIO modes.
 */
typedef enum
{
    GPIO_MODE_OUTPUT=0,     /**< GPIO as output. */
    GPIO_MODE_INPUT         /**< GPIO as input. */
} gpio_mode_t;

/**
 * \brief GPIO pin configuration.
 */
typedef struct
{
    gpio_mode_t mode;
} gpio_config_t;

/**
 * \brief Initialization routine of a GPIO pin.
 *
 * \param[in] pin is the GPIO pin to initialize.
 *
 * \param[in] config is the configuration to initialize the GPIO pin.
 *
 * \return The status/error code.
 */
int gpio_init(gpio_pin_t pin, gpio_config_t config);

/**
 * \brief Sets the state of a given output GPIO pin.
 *
 * \param[in] pin is the GPIO pin to set the state.
 *
 * \param[in] level is the new state of the given GPIO pin. It can be:
 * \parblock
 *      - GPIO_STATE_HIGH
 *      - GPIO_STATE_LOW
 *      .
 * \endparblock
 *
 * \return The status/error code.
 */
int gpio_set_state(gpio_pin_t pin, bool state);
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

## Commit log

2021-04-02 hardware: Importing FloripaSat-1 TTC altium project #2
    [0_architecture.schdoc, 1_interface.schdoc, 2_topology.schdoc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]
2021-04-02 hardware: schematics: Changing sheets template and parameters #2
    [0_architecture.schdoc, 1_interface.schdoc, 2_topology.schdoc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]
2021-04-02 hardware: schematics: Adding architecture diagram #2
    [0_architecture.schdoc]
2021-04-02 hardware: schematics: Updating interface sheet organization #2
    [1_interface.schdoc]
2021-04-02 hardware: schematics: Updating radios sheets organization and documentation #2
    [5_main_radio.schdoc, 6_beacon_radio.schdoc]
2021-04-04 hardware: schematics: Updating sheets color #2
    [1_interface.schdoc, 2_topology.schdoc]
2021-04-04 hardware: schematics: Updating radios signals and harness nomenclature #2 #3
    [5_main_radio.schdoc, 6_beacon_radio.schdoc]
2021-04-04 hardware: schematics: Adding voltage/current sensors and I2C buffer #4 #5 #6
    [4_mcu_beacon.schdoc]
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2021-04-06 hardware: schematics: Updating architecture diagram #2
    [0_architecture.schdoc]
2021-04-06 hardware: schematics: Updating Beacon MCU harness and adding watchdog timer #8 #13
    [4_mcu_beacon.schdoc]
2021-04-06 hardware: schematics: Adding serial, GPIO and additional interfaces #1 #2 #10
    [4_mcu_beacon.schdoc]
2021-04-06 hardware: schematics: Removing reference legacy radio circuit #2
    [6_beacon_radio.schdoc]
2021-04-06 hardware: schematics: Adding the new independent MCU and its auxiliary circuits #7
    [3_mcu_main.schdoc, 4_mcu_beacon.schdoc]
2021-04-06 hardware: schematics: Updating the topology diagram #1 #2
    [2_topology.schdoc]
2021-04-06 hardware: schematics: Adding new connectors for each MCU/radio modules #1
    [1_interface.schdoc]
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2021-04-08 hardware: schematics: Updating the radios nomenclature #3
    [2_topology.schdoc, 3_mcu_main.schdoc, 3_mcu_radio_0.schdoc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]
2021-04-08 hardware: schematics: Updating nomenclature and adding harness #2 #3
    [2_topology.schdoc, 3_mcu_radio_0.schdoc, 4_mcu_radio_1.schdoc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]
2021-04-09 hardware: schematics: Adding PC-104 new buses #1 #2
    [1_interface.schdoc, 2_topology.schdoc, 3_mcu_radio_0.schdoc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]
2021-04-09 hardware: schematics: Adding antenna and debug headers #1 #2
    [1_interface.schdoc, 3_mcu_radio_0.schdoc, 4_mcu_radio_1.schdoc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]
2021-04-09 hardware: schematics: Synchronizing the sheets ports and harness #2
    [1_interface.schdoc, 2_topology.schdoc, 3_mcu_radio_0.schdoc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]
2021-04-09 hardware: schematics: Fixing sheets typos and legacy labels/parameters #2
    [1_interface.schdoc, 3_mcu_radio_0.schdoc, 4_mcu_radio_1.schdoc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]
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2021-04-10 hardware: Updating the schematic template of all sources and adding author, revision and project code parameters to project #2
    [0_architecture.schdoc, 1_interface.schdoc, 2_topology.schdoc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]
2021-04-10 firmware: system: sys_log: Fixing the number of the UART port #12
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2021-04-11 hardware: schematics: Adding ESD resistor to M3 screw hole
    [0_architecture.schdoc, 1_interface.schdoc]
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2021-04-11 hardware: libraries: Adding new connectors and ICs #17
    [ttc2_project.prjpcb]
2021-04-11 hardware: schematics: Replacing interface components with the new library #18
    [1_interface.schdoc, 2_topology.schdoc]
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2021-04-11 hardware: schematics: Replacing components with the new library #18
    [1_interface.schdoc, 3_mcu_radio_0.schdoc, 4_mcu_radio_1.schdoc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]
2021-04-12 hardware: schematics: Fixing wrong crystal label assignment
    [3_mcu_radio_0.schdoc, 4_mcu_radio_1.schdoc]
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2021-04-14 hardware: schematics: Removing unnecessary pull-up resistors of the I2C sense bus
    [3_mcu_radio_0.schdoc, 4_mcu_radio_1.schdoc]
2021-04-14 firmware: drivers: spi: Fixing the CS pins initialization #12
    [spi.c]
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2021-04-15 hardware: schematics: Fixing label typos
    [1_interface.schdoc, 4_mcu_radio_1.schdoc]
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2021-04-15 hardware: outputs: Updating schematic sheets after bugfixes
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2021-04-23 hardware: layout: Improving shielding vias and MCX connectors
    [1_interface.schdoc, ttc2_project.prjpcb]
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2021-04-24 hardware: outputs: Adding preliminary documentation for early revision
    [board_bom.xls, ttc2_project.prjpcb]
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2021-05-02 hardware: schematics: Changing LED colors for radio 1
    [4_mcu_radio_1.schdoc]
2021-05-02 hardware: schematics: Updating antenna picoblades for better power handling
    [1_interface.schdoc]
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2021-05-02 hardware: layout: Fixing power track thickness and running DRC #22 #30
2021-05-02 hardware: schematics: Adding interrupt pin to OBDH SPI interfaces #35
    [1_interface.schdoc, 3_mcu_radio_0.schdoc, 4_mcu_radio_1.schdoc]
2021-05-02 hardware: schematics: Removing testpoints and adding pull-up resistors to sensor alert #33 #36
    [1_interface.schdoc, 3_mcu_radio_0.schdoc, 4_mcu_radio_1.schdoc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]
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2021-05-02 hardware: layout: Fixing silkscreen collision
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2021-05-02 hardware: outputs: Adding fabrication and assembly files #31
    [board_gerber.GBL, board_gerber.GBO, board_gerber.GBP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]
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2021-05-05 hardware: Updating project file tree to include new draftsman source
    [ttc2_project.prjpcb]
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2021-05-12 hardware: prjpcb: Disabling rooms during ECO generation #28
    [ttc2_project.prjpcb]
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2021-05-13 firmware: drivers: si446x: Fixing the initialization and changing the SPI port
    [si446x.c]
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2021-06-03 hardware: libraries: Updating ID and descriptions of components on the schematic library hardware: sources: Updating schematics and layout with new component parameters hardware: outputs: bom: Fixing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
    [1_interface.schdoc, 3_mcu_radio_0.schdoc, 4_mcu_radio_1.schdoc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]
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2021-06-15 hardware: layout: Updating PCB color and adding teardrops. close #40
    [ttc2_project.prjpcb]
2021-06-15 hardware: fabrication: Updating all fabrication files, deleting old BOM #47
    [board_bom_ttc2.xlsx, bom.xls]
2021-06-15 hardware: outputs: Updating camtastic and adding to project tree #47
    [ttc2_project.prjpcb]
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2021-06-15 hardware: fabrication: Generating again fabrication files after last DRC check #47
    [board_bom_ttc2.xlsx]
2021-06-15 hardware: Updating project file, outjob and draftsman source file
    [ttc2_project.prjpcb]
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2021-08-12 firmware: tests: devices: temp_sensor: Fixing the test #54
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2021-08-14 firmware: tests: devices: Fixing the radio unit test compilation
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2021-12-20 firmware: drivers: sx127x: Implementation of the register access functions, and general fixes #60
    [sx127x.c]
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2022-04-01 firmware: drivers: uart: Implemented the report error for read rx buffer function #61
    [uart.c]
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2022-04-08 firmware: drivers: uart: Implemented enable/disable functions for uart interruption resolves #61
    [uart.c]
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2022-04-16 firmware: drivers: uart: Fixing code errors #61
    [uart.c]
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2022-04-19 firmware: tests: devices: Stored the returned value from wrap_wdt_init resolved #67
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2022-04-23 firmware: drivers: uart: Updating the source files version and, minor fixes and improvements #61
    [uart.c]
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2022-04-23 firmware: drivers: sx1271x: Fixing compilation errors #60
    [sx127x.c, sx127x_gpio.c]
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2022-04-26 firmware: devices: antenna: Fixing the init test for the antenna test #70 The init function could not find the config flag.
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2022-04-30 firmware: system: Fixing the hardware version control pins
    [system.c]
2022-04-30 firmware: devices: leds: Fixing the system LED pin
    [leds.c]
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2022-05-09 firmware: drivers: si446x: Fixing the config file include
    [si446x.c]
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2022-05-11 firmware: drivers: si446x: Fixing function definition #76
    [si446x.c]
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2022-05-15 firmware: drivers: si446x: Fixing return value from standby mode function #77
    [si446x.c]
2022-05-15 firmware: devices: radio: Fixing if statement #78
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2022-05-15 firmware: tests: devices: Fix #78 radio unit test
2022-05-17 firmware: drivers: ina22x: Minor fix #19
2022-05-17 firmware: devices: watchdog: Fixing MISRA-C 2012 rule
2022-05-17 firmware: drivers: Fixing MISRA-C 2012 rules #80
    [adc_delay.c, ina22x.c]
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2022-05-23 firmware: drivers: spi_slave: Fixing initialization variable names #58
    [spi_slave.c]
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2022-05-23 firmware: drivers: spi_slave: Create missing function declarations #58
    [spi_slave.c]
2022-05-25 firmware: drivers: spi_slave: Fixing errors #58
    [spi_slave.c]
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2022-06-07 firmware: drivers: ina22x: Fixing function names #19
    [ina22x.c]
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2022-06-21 firmware: tests: drivers: Minor fixes in the INA22x driver unit test #87
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2022-06-25 firmware: drivers: ina22x: Fixing the driver according to the unit tests #19
    [ina22x.c]
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2022-06-29 firmware: drivers: ina22x: Fixing and improving the driver according to the unit tests #19
    [ina22x.c]
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2022-08-02 firmware: drivers: ina22x: Minor fixes #19
    [ina22x.c]
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2022-08-07 firmware: drivers: ina22x: Fixing returning type from measurement functions #19
    [ina22x.c]
2022-08-08 firmware: tests: mockups: drivers: Fixes to the ina22x mockup #19, #20
2022-08-08 firmware: devices: power_sensor: Fixing i2c speed clock parameter from config structs #20
    [power_sensor.c]
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2022-08-29 firmware: devices: power_sensor: Fixing uc current scale #20
    [power_sensor.c]
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2022-08-30 firmware: tests: drivers: Fixing typo in Makefile
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2022-09-27 firmware: drivers: spi: Fixing pin assignment and configuration parameters
    [spi.c]
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2022-10-02 firmware: drivers: si446x: Minor fixes
    [si446x.c, si446x_gpio.c]
2022-10-03 firmware: devices: leds: Fixing the pinout of the system/fault LEDs
    [leds.c]
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2022-11-01 firmware: drivers: spi_slave: Fixing driverlib bug #58
    [spi_slave.c]
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2022-11-04 firmware: drivers: gpio: Fixing MISRA-C 2012 rules #104
    [gpio.c, gpio.h]
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2022-12-06 firmware: drivers: isr: Fix formatting #85
    [isr.c]
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2023-02-11 firmware: drivers: spi_slave: General improvements/fixes to driver #58
    [spi_slave.c]
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2023-02-13 firmware: drivers: uart: Adding missing keyword in function definition #61
    [uart.c]
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2023-02-15 firmware: drivers: spi_slave: Adding Missing group end for doc #115
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2023-02-16 firmware: tests: drivers: Fixing the Makefile
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2023-02-20 firmware: drivers: spi_slave: Fixing log typos #58
    [spi_slave.c]
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2023-03-07 firmware: devices: eps: Fixes for eps device header #118
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2023-03-08 firmware: Updating the version number and minor fixes #122
    [config.h, eps.c]
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2023-03-20 firmware: app: tasks: Fixing expression for switch #122
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2023-03-22 firmware: drivers: isis_antenna: Fixing tca4311a wrong parameter during initialization, closes #101
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2023-03-22 firmware: drivers: tca4311a: Fixing status enum description
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2023-04-17 firmware: Updating firmware version and minor fixes
    [config.h, obdh.c]
2023-04-17 firmware: tests: devices: Fixing warnings in the OBDH device test
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2023-05-23 firmware: drivers: isr: Fixing spi in RX only #125
    [isr.c]
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2023-09-05 firmware: drivers: isis_antenna: Importing buffer fix #138
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2023-09-27 firmware: tests: devices: Adding missing sys_log wraps #124
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2023-10-05 firmware: drivers: isis_antenna: Inverting antenna response bytes #138
    [isis_antenna.c]
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2023-10-24 firmware: devices: obdh: Fixing wrong return code #124
    [obdh.c]
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2023-10-28 firmware: Minor fixes and updating the version number of the modified files
    [config.h, isr.c, obdh.c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]
2024-01-16 firmware: drivers: si446x: Adding delay during configuration to avoid radio resets #145
    [si446x.c]
2024-01-16 firmware: devices: radio: Fixing radio_available function description #145
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2024-01-30 firmware: tests: drivers: Updating si446x test, resolves #146
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2024-02-28 firmware: devices: radio: Using si446x mutex on radio functions, resolves #134
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2024-05-16 firware: app: tasks: Fixing device id struct value #146
2024-06-04 firmware: drivers: si446x: Adding error directive to force select target radio #146
    [si446x.c]
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2024-08-08 firmware: drivers: Fixing FIFO configuration size, closes #145
    [si446x.c]
2024-08-08 firmware: devices: temp_sensor: Fixing if statement for celsius conversion
    [temp_sensor.c]
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2024-08-08 firmware: devices: temp_sensor: Correcting TEMP_SENSOR_ADC_PORT macro
2024-08-08 firmware: devices: Adding fixes from obdh
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2024-08-09 firmware: tests: drivers: Fixing radio includes #76
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2024-09-03 doc: user_manual: chapters: Fixing pin setup typos
2024-09-06 firmware: system: Implementing system reset counter #156
    [system.c]
2024-09-06 firmware: devices: leds: Adding firmware fix for #113
    [leds.c]
2024-09-06 firmware: tests: devices: Updating obdh with reset_device #156
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2024-09-06 firmware: tests: devices: Fixing leds gpio pins
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2024-09-12 firmware: devices: obdh: Fixing reset parameter, closes #156
    [obdh.c]

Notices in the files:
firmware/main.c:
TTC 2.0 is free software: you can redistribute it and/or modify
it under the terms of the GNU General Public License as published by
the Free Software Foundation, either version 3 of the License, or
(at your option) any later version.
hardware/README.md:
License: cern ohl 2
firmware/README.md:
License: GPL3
